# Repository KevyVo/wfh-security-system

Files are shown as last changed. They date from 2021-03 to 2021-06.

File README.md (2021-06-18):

# Work From Home Security System Documentation

## Summary
Due to COVID-19, in early spring my internship was forced to transition into a remote and virtual experience. Whenever I had a meeting, my housemates would find ways to disturb me, whether by knocking loudly, or by walking in unannounced. I searched everywhere for a smartlock that would be able to alert people outside that I was in a meeting. Unfortunately, I could not find anything that fit all my needs. Fortunately, being the engineering student I am, I knew what I had to do. It was time to bring this idea into existince and build it myself. 

<!--- ! This is the scanning picture [Project_Image](https://github.com/KevyVo/Smart-Doorlock/blob/table/Images/finger.jpg) -->
lock

## Table of Contents

1. [Demo/Features](https://github.com/KevyVo/wfh-security-system#demofeatures)
2. [Installation/Instructions](https://github.com/KevyVo/wfh-security-system#installationinstructions)
3. [Cloud Architecture](https://github.com/KevyVo/wfh-security-system#cloud-architecture)
4. [Embedded Software](https://github.com/KevyVo/wfh-security-system#embedded-software)
   1. [High-Level State Diagram](https://github.com/KevyVo/wfh-security-system#high-level-state-diagram)
   2. [Low-Level Flowchart](https://github.com/KevyVo/wfh-security-system#low-level-flowchart)
   3. [User Table Interaction Diagram](https://github.com/KevyVo/wfh-security-system#user-table-interaction-diagram)
   4. [File Structure Directory](https://github.com/KevyVo/wfh-security-system#file-structure-directory)
   5. [Custom Libraries](https://github.com/KevyVo/wfh-security-system#custom-libraries)
5. [3D Printed Parts and CAD Model](https://github.com/KevyVo/wfh-security-system#3d-printed-parts-and-cad-model)
   1. [Front I/O](https://github.com/KevyVo/wfh-security-system#front-io)
   2. [Internal Housing](https://github.com/KevyVo/wfh-security-system#internal-housing)
6. [Electrical](https://github.com/KevyVo/wfh-security-system#electrical-1)
   1. [Wiring Diagram](https://github.com/KevyVo/wfh-security-system#wiring-diagram)
   2. [Wiring Tables](https://github.com/KevyVo/wfh-security-system#wiring-tables)
7. [Materials and Equipment](https://github.com/KevyVo/wfh-security-system#materials-and-equipment)
   1. [Equipment](https://github.com/KevyVo/wfh-security-system#equipment)
   2. [Materials](https://github.com/KevyVo/wfh-security-system#materials)
8. [Troubleshooting and Common Problems](https://github.com/KevyVo/wfh-security-system#troubleshooting-and-common-problems)

## Demo/Features

My work from home security system, aid in alot more ways then just a smart door lock. There would be a live gif and a small explantion for all features:

1.  Remote Arming/Disarming from serverless site</br><details> 
     <summary>Click for Live Demo</summary>
     
     ### Override Trigger
     1. In the gif the main.py file is waiting for a trigger when the user want to diable the alarm system.
        - unlock
     2. In the gif the main.py file is waiting for a trigger when the user want to arm the alarm system.
        - lock
   </details>

2.  Live updates from serverless site</br><details> 
     <summary>Click for Live Demo</summary>
     
     ### Live update
     - Will update all information relating to the last or cuurent state of the door, either by moblie browser or web browser.
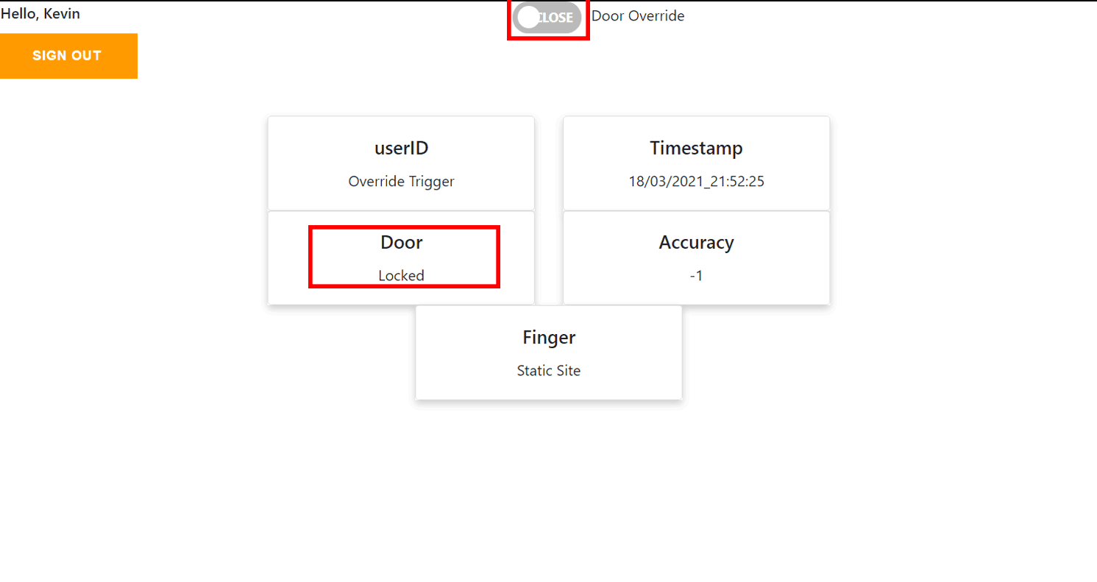
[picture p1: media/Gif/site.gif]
web
       - 
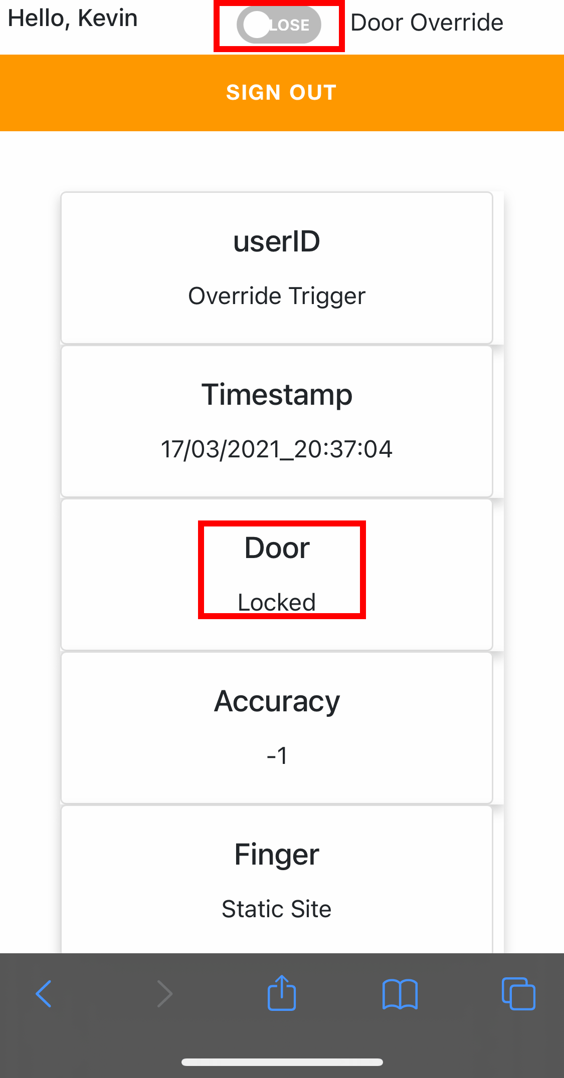
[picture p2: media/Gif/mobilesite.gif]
       - 
   </details>

3.  Google calendar API</br><details> 
     <summary>Click for Live Demo</summary>
     
     ### Google Calendar
     - This will read continously from your google work calendar and alert other outside your door not to distrub during these hours.
       - google
   </details>

4.  Autonomous Motion Light/System Sensor</br><details> 
     <summary>Click for Live Demo</summary>
     
     ### Light/System Sensor
     - The light and security system will turn on with motion and turn off after 5 mins of no activity. The sensor will work in the darkest condtions.
       - dark
   </details>

5.  Biometric Authentication</br><details> 
     <summary>Click for Live Demo</summary>
     
     ### Fingerprint Scanner
     - Authenticate authorize user to gain access to the room with their pre-regsiter fingerprint, the light will also blink a certain colour depending on the assessment. It will also save any fail fingerprint on local storage for identifying potential unauthorized events.
       - Correct Fingerprint (Blink Green)
       - correct
       - Incorrect Fingerprint (Blink Red)
       - Incorrect
   </details>

6.  Excceded Timeout</br><details> 
     <summary>Click for Live Demo</summary>
     
     ### Timeout
     - Will set a timeout of 5 mins after 3 continous authenication failures, every addtion failure will be (timeout= tries * 5 mins). This will reset after one correct authernication. It will also save any fail fingerprint on local storage for identifying potential unauthorized events.
       - timeout
   </details>

7.  Forced Entry Detection</br><details> 
     <summary>Click for Live Demo</summary>
     
     ### Forced Entry Detection
     - Will sound an alarm once the door is open with any proper autheication or break in. The alarm will only turn off once a authenticated fingerprint has reset the alarm.
       - fsd
   </details>

8.  E-mail alerts</br><details> 
     <summary>Click for Live Demo</summary>
     
     ### Alerts
     - There are 3 events that will send e-mails on
      1. Force Entry Dectection Triggered
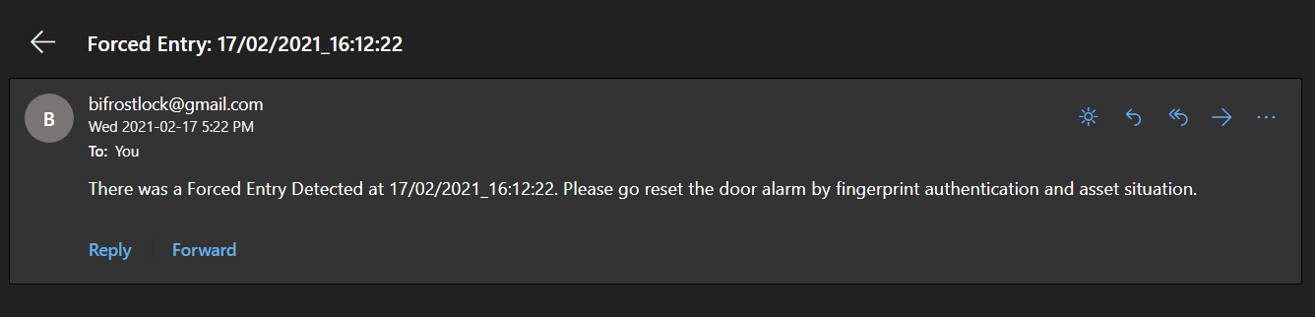
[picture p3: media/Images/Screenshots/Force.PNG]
force
          + 
      2. Correct fingerprint to deactivate the alarm
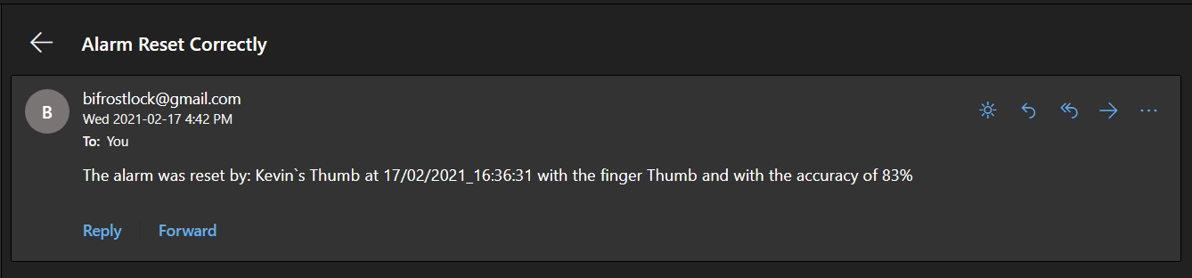
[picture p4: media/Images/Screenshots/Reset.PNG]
reset
          + 
      3. Fail fingerprint with the fail printed attached to e-mail (In real e-mail the fingerprint would not be blurred)
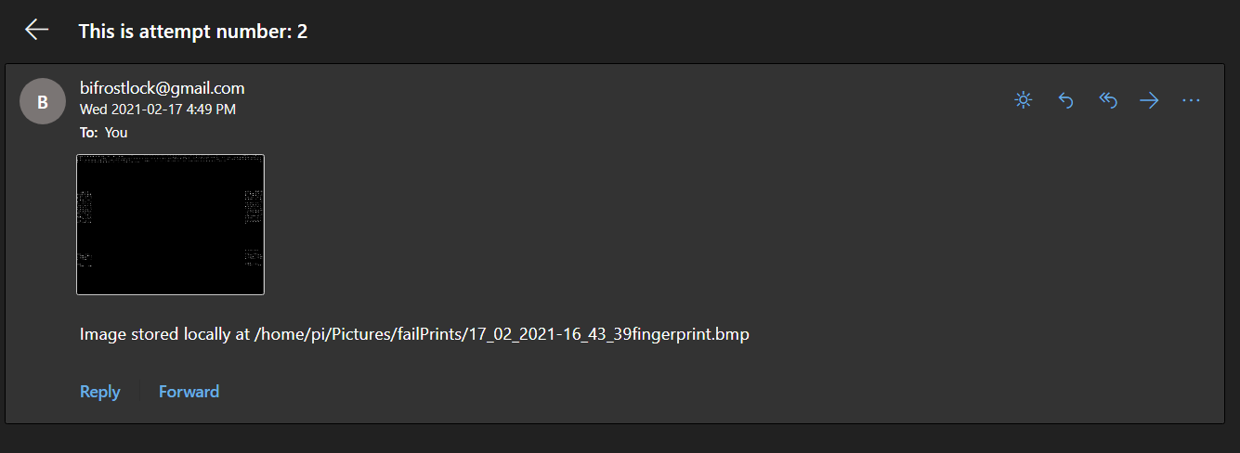
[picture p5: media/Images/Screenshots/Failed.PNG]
fail
          + 
   </details>

9.  Logging events into database</br><details> 
     <summary>Click for Live Demo</summary>
     
     ### Logging
     - Will recored all events of the state of the door in a database for security purposes.
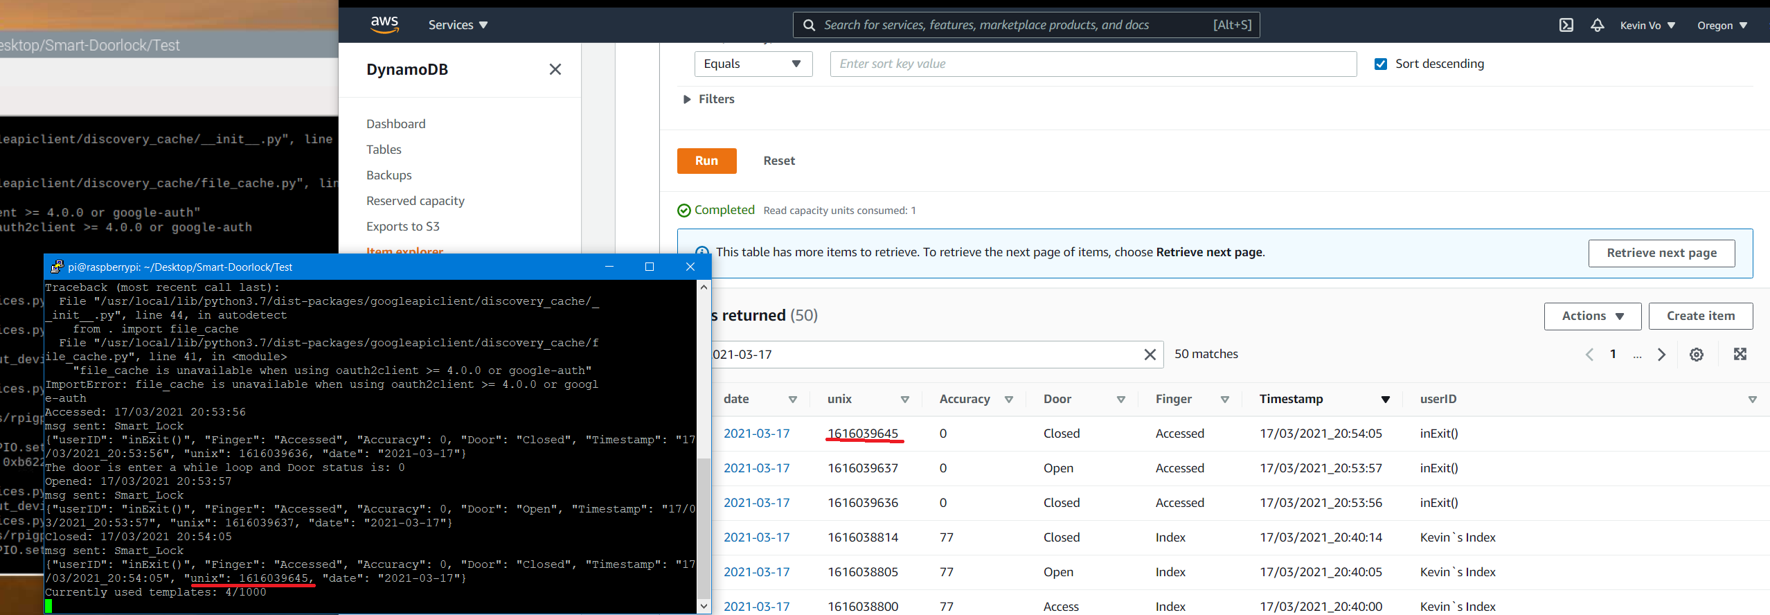
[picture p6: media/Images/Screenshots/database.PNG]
database
       - 
   </details>

10.  Motion alert</br><details> 
     <summary>Click for Live Demo</summary>
     
     ### Logging
     - Red and Green light will blink simultaneously if there is motion on the other side of the door.
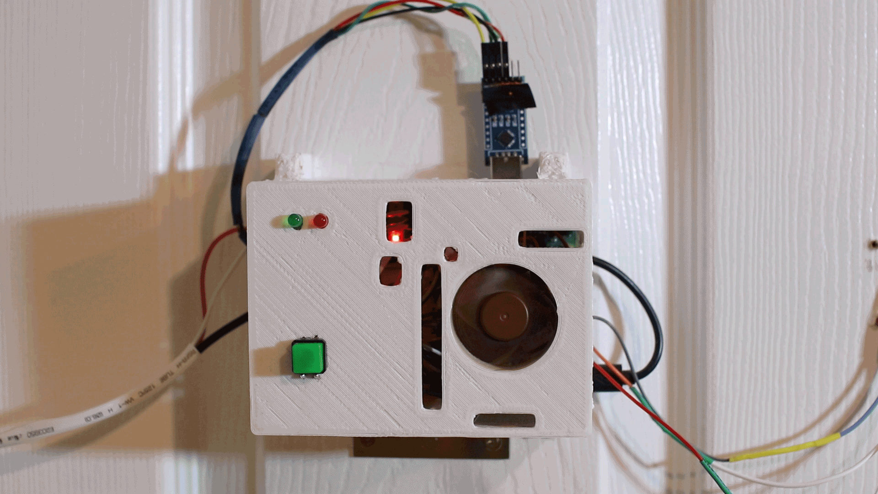
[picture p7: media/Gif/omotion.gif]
motiond
       - 
   </details>

11.  Daytime/Nightime Mode</br><details> 
     <summary>Click for Live Demo</summary>
     
     ### Sound Change
     1.  8AM - 8PM the alarm buzzer will make sound when in use
     2.  8PM - 8AM the alarm buzzer will be disable for nightime use
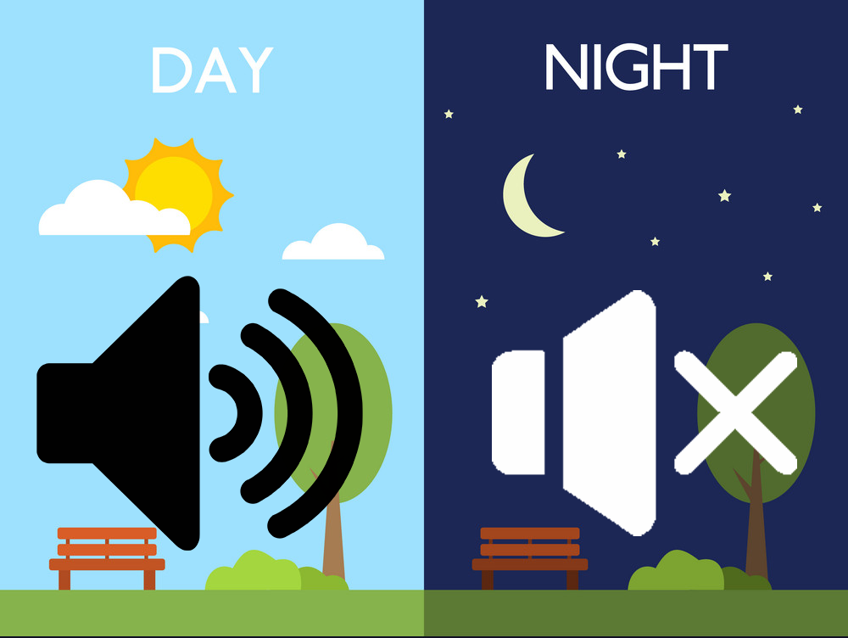
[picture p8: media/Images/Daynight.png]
dn
         - 
   </details>

## Installation/Instructions

**Youtube video**
Coming Soon
<!--- [![IMAGE ALT TEXT HERE](http://img.youtube.com/vi/YOUTUBE_VIDEO_ID_HERE/0.jpg)](http://www.youtube.com/watch?v=YOUTUBE_VIDEO_ID_HERE) -->

Since this project is made up of cloud, electrical and software engineering. I have split up instructions into their own categories to make it easier to follow. 
The React static site has it own separate [repo](https://github.com/KevyVo/wfh-serverless-site), which will appear again in the step below when needed.

Please follow these sequence of instructions in **order** by clicking on the collapsable tabs:</br> **Click on any pictures/GIFs to enlarge them**

1.  <details>
     <summary>Click for General Setup Instruction</summary>
     
     ### General Setup
     1. Gather the materials and make sure you have aquired or have access to the required equipment, found [here](https://github.com/KevyVo/Smart-Doorlock#materials-and-equipment)
     2. Start the 3D print of the Front and Back IO, these prints will take about 1-2 days to 3D print, click here for [files](https://github.com/KevyVo/Smart-Doorlock/tree/master/Cad)
        + There should be 4 total seprate prints
        + These prints will take 1-2 days depending if you deviate from the recommended print settings
        + If you use prusasilcer like me, I highly recommend using these settings here
        + You can find the files here 
     3. Setup the Raspberry Pi
        + RECONMEND: I would use remote access methods like VNC Viewer or SSH, it makes it much easier to control the pi instead of direct connection
        1. Please follow this setup tutorial [here](https://www.tomshardware.com/reviews/raspberry-pi-headless-setup-how-to,6028.html), once completed move onto step b
        2. Please clone this repo to the pi <br/>```git clone https://github.com/KevyVo/Smart-Doorlock ```
        3. cd into the the requirements folder<br/> ```cd Smart-Doorlock/requirments/```
        4. Install the requirements<br/> ```pip install -r require2.txt -r require3.txt```
           + You can also do this inside a virtual environment(venv) if you want
     4. Move onto the Electrical Instructions
   </details>
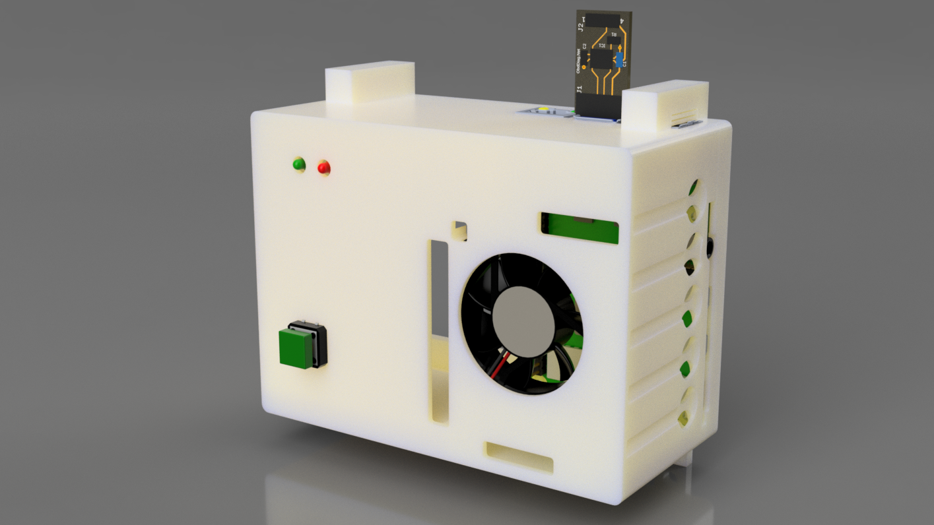
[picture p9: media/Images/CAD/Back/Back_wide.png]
        &nbsp;&nbsp;&nbsp; 

2.  <details>
     <summary>Click for Electrical Instruction</summary>

     ### Electrical

     For a larger image of the wiring diagram and wiring table, please click [here](https://github.com/KevyVo/Smart-Doorlock#electrical-1)

     1. I would recomend testing all of your components indivdially first to see if there are any defects/problems
        1. Go to the Test directory
        2. Select desired component base on the python file
        3. Follow the comment instrutions in the py file of what gpio pins to connect to
        + If the python file does not run in the ide, run it in the terminal using python3 command</br> ```python3 component_name.py```
        + By doing this you will understand how each component behaves and interacts with each other, and assures that it is free of defect
     2. cd into the ```cd Smart-Doorlock/Components/pyfingerprint/example_enroll```
        + I am still working on a feature to enroll your fingerprint using a button on the static- please stay posted! For now, use this method, unless you want to help the project add to it :)
     3. Run the file either in the terminal or ide
        + Congrats! Your fingerprint has been enrolled locally to the system
     4. When connecting the dupoint connectors, make sure you can disconnect the male to female cable apart. This will be useful for mounting installtion later.
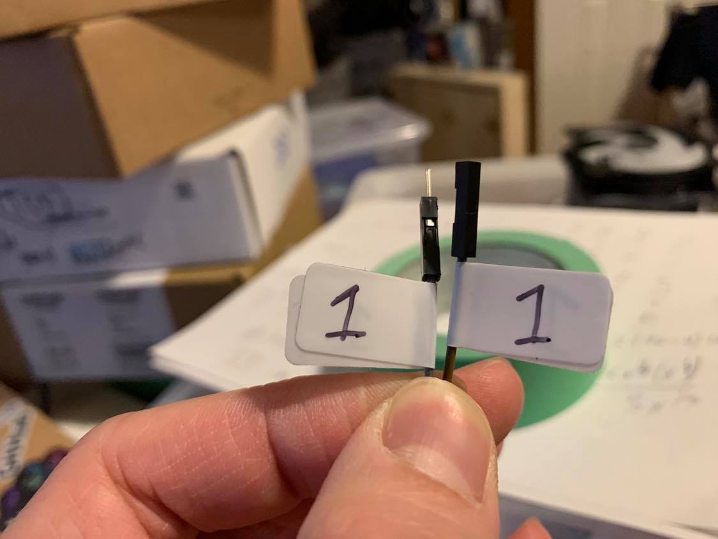
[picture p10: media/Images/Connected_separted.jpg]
        + 
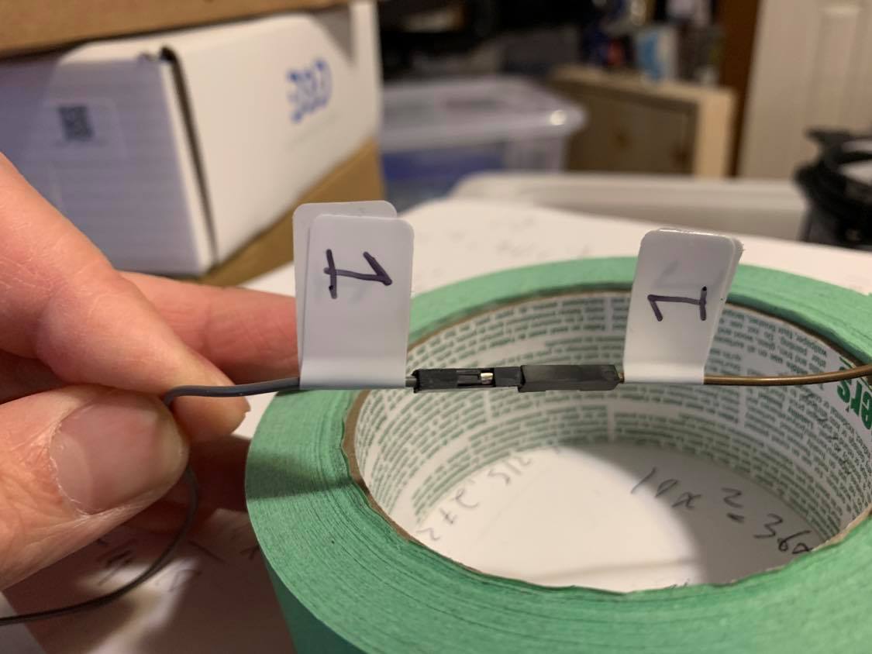
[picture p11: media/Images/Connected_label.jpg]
        + 
     5. Label all cables like this; it make the rewiring installtion easier later on
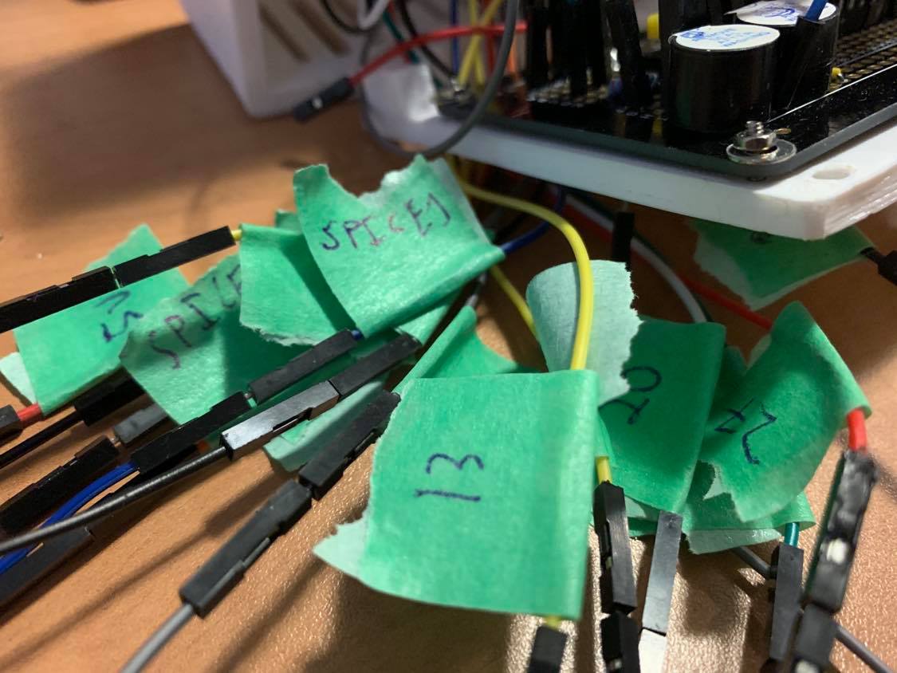
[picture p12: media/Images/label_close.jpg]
        + 
     6. Connect and solder all the electical connections using this diagram and connection tables found here
        + RECOMMENDED: I personally connect all the connections and components on a protyping breadboard before moving onto the solderable PCB
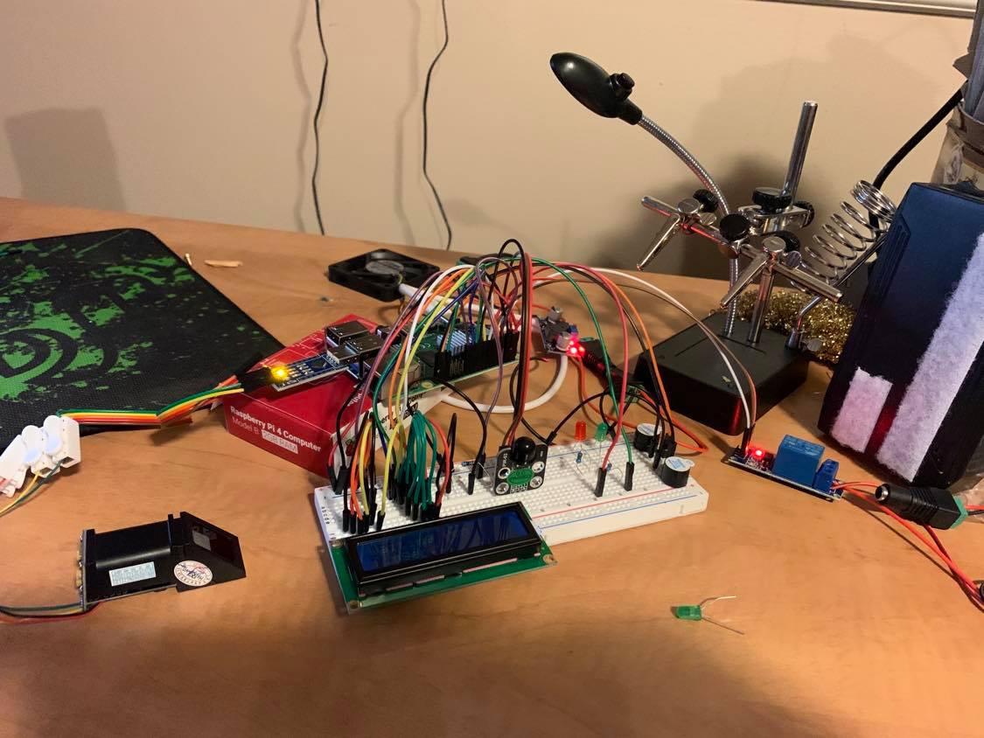
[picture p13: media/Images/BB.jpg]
        + 
        + Run the script ```non-cloud base script```
     7. Run the non cloud base script, to test how all the components will work all together
        + If you see any warnings that do not effect your program, just ignore them for now
     8. If everything was successful please move onto Cloud instructions 
   </details>

   &nbsp;&nbsp;&nbsp; 

3.  <details>
     <summary>Click for Cloud/Software Instruction</summary>

     If you want to read more about how the cloud architecture works please click [here](https://github.com/KevyVo/Smart-Doorlock#cloud-architecture)

     If you want to read more about the flow of the software, please click [here](https://github.com/KevyVo/Smart-Doorlock#embedded-software)

     ### AWS Setup
      1. Sign up for a AWS account (if you already have a account you can skip this step)
         + Follow this [guide](https://docs.aws.amazon.com/polly/latest/dg/setting-up.html) for help if needed 
         + AWS is free if you stay below the free teir limit (we won`t even get close to hitting the limit in this project); AWS is also cheap for personal use if you go over the limit. 
      2. Setup a new IAM user- make sure to give programmatic access and console access and AdministratorAccess policy (you can add the appropriate policy if you know what you are doing)
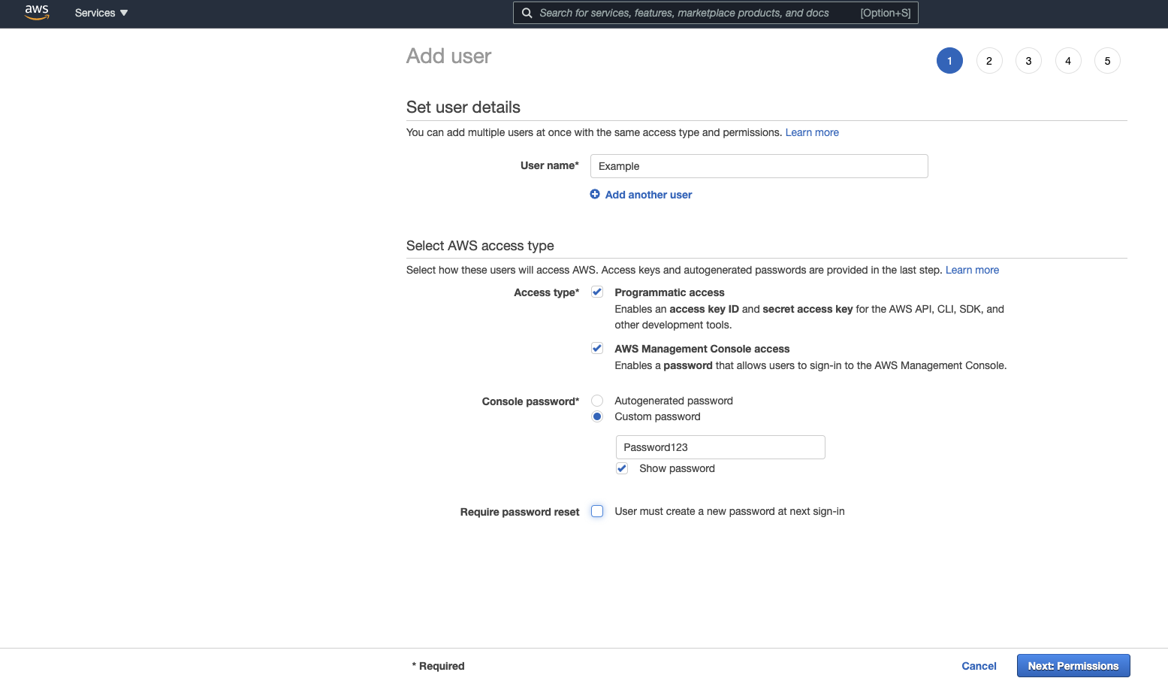
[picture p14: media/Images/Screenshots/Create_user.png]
         + 
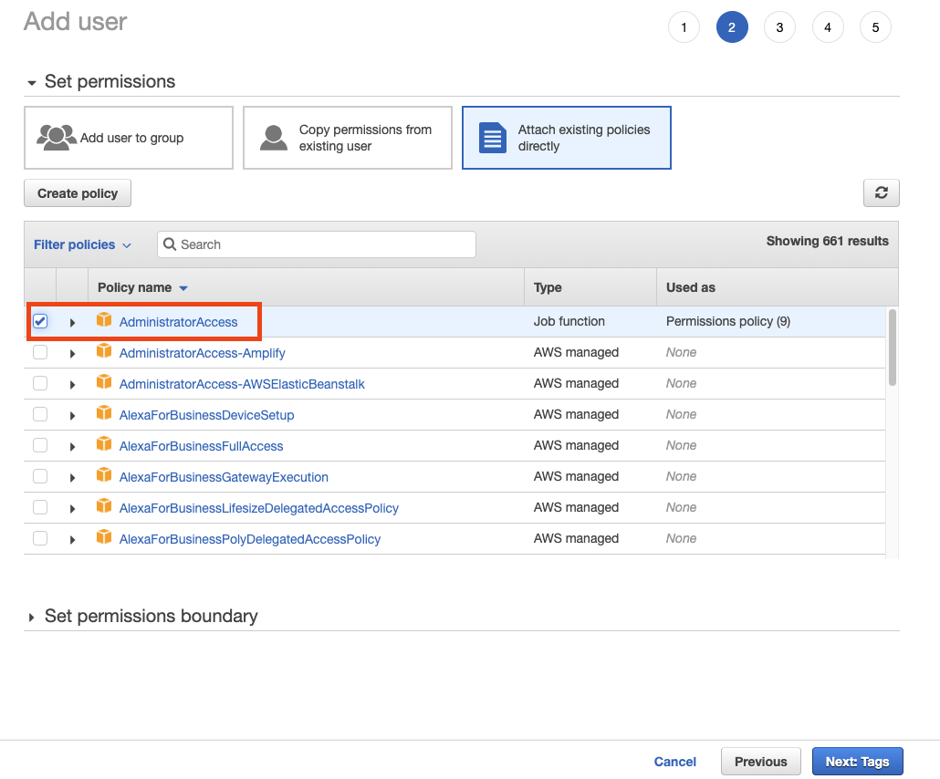
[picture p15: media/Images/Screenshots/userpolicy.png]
policy
         +   
      3. Retrieve the credential for later use
      4. Open up the terminal on the Pi and enter:</br>```aws configure```
      5. Enter that AWS account credentional; please refer to the screenshot for futher assitance and [link](https://docs.aws.amazon.com/polly/latest/dg/setup-aws-cli.html)
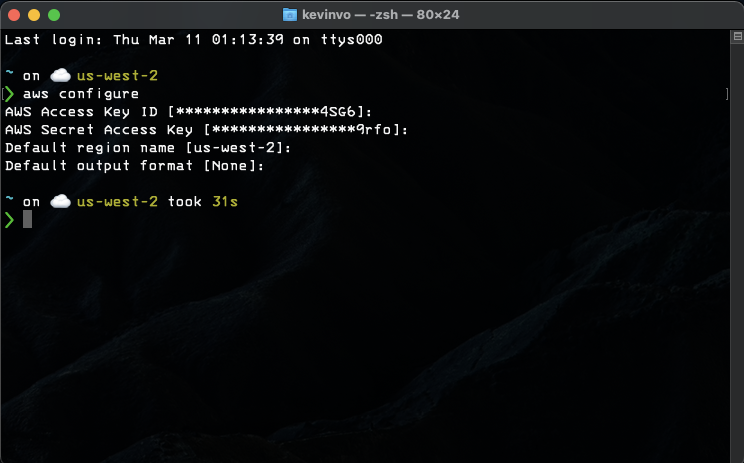
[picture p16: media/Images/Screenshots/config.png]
config
         + 
     ### AWS Iot Core (PubSub)
      1.  We need to sign into the aws console and go to AWS Iot core
      2.  Go to Manage->Things->Regsister a thing
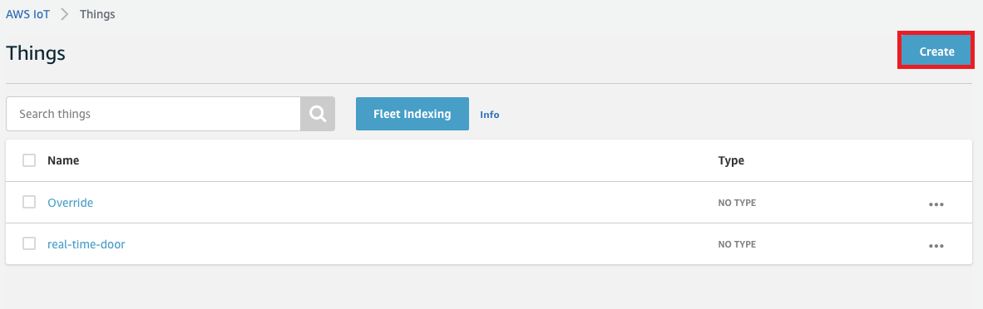
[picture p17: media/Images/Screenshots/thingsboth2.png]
things
          + 
      3.  Click create a single thing and Give your thing name, scroll down and tap on the Next button and then you are immediately offered the one-click certificate generation option. An individual X.509 certificate per device is the recommended way of interacting with AWS IoT services from devices, offering the ability to burn the private key into the device upon enrolment that is then never transferred across the internet alongside requests, a security win. Download the certificate and private key for each device, and also a root CA. Make sure to hit that activate button so the certificate can be used. finish the process by clicking on the “Done” button.
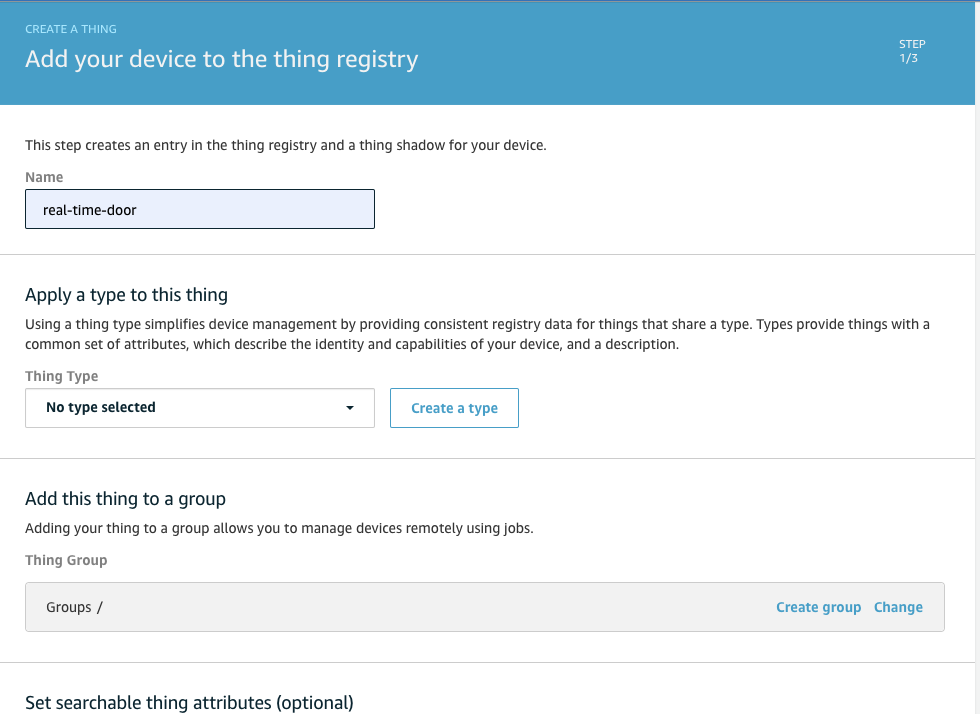
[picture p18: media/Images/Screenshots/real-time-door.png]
          + 
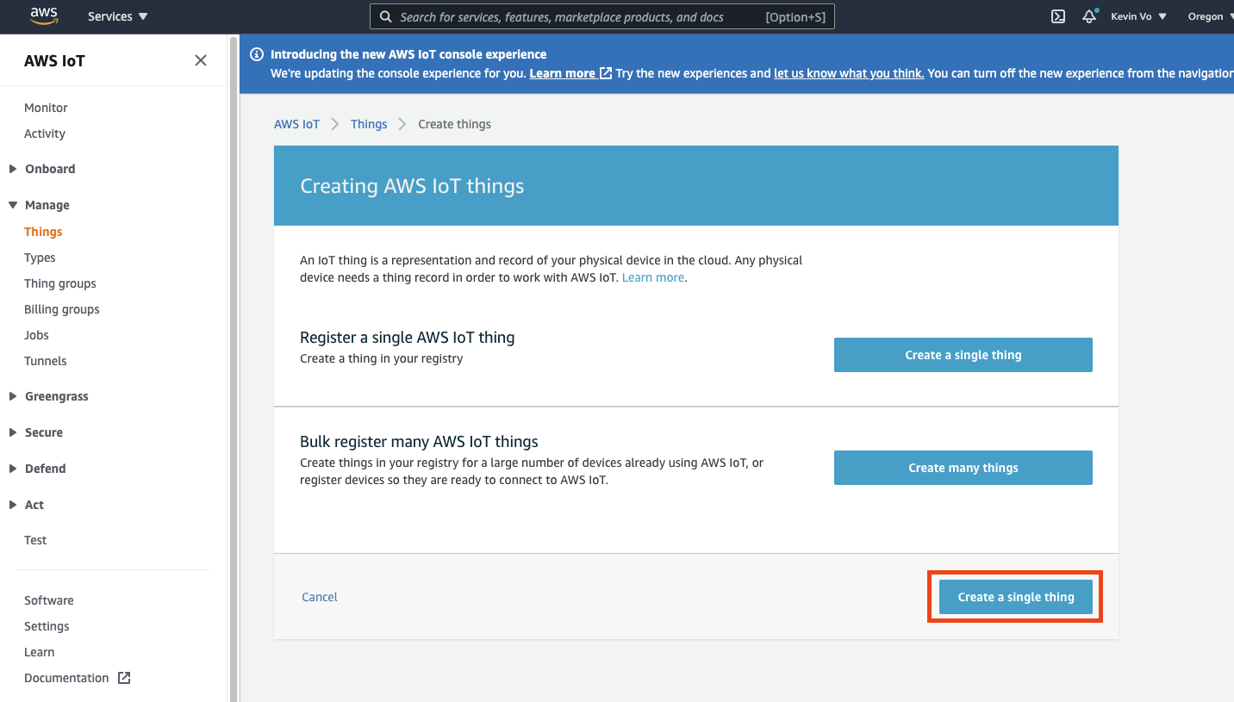
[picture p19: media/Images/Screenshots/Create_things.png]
          + 
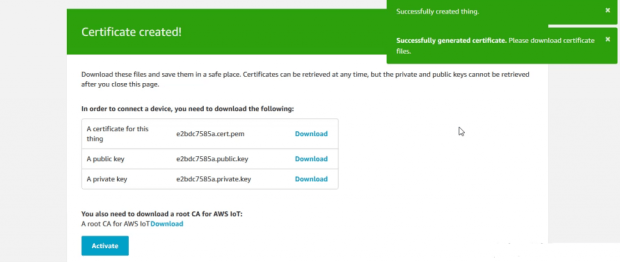
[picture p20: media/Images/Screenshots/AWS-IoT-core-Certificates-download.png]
cert
          + 
      4.  Next point is to create and attach a policy to the certificate, authorizing the authenticated device to perform IoT actions on IoT resources. for this tap on the “secure” tab from the AWS IoT menu which is on the left side, later go for the policies section. Now tap on the button named “Create” which is on the top right corner beside the iot-notifications Icon. give your policy name and fill the fields(Action, Resource ARN ) with a star “*” and check to Allow for Effect option then press the “create” button.
      5.  Now tap on the certificates section which is right above the policies section, You will see a certificate which you have created earlier, tap on the three dots and choose to attach the policy, a pop will come showing your existing policies, check on the recent policy that you have created and attach. That’s it you have successfully created a thing, generated a certificate and attached policy to it.
      6.  You can find the endpoint here
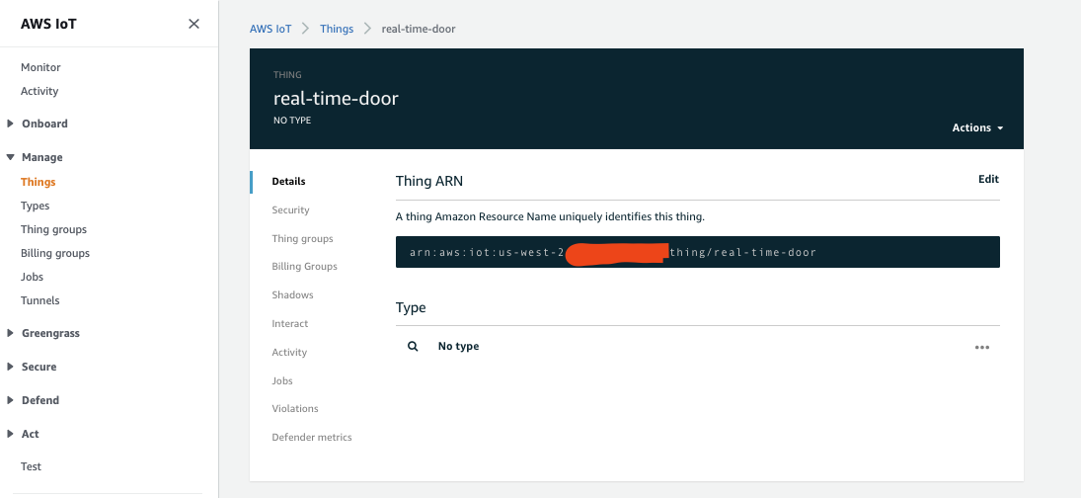
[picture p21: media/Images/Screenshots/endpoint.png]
endpoint
          + 
      7.  I recommend putting all the files/cerficates in the empty directory I premade called "Credtionals"
          + The endpoint can found here
      8.  Fill out the appropriate lines out with the correct pathing in the main.py</br>
            ```
            awshost = "xxxxxxxxxxxxxx-ats.iot.us-east-2.amazonaws.com" # Endpoint
            awsport = 8883 # Port no. 
            clientId = "xxxxxxxx" # Thing_Name
            thingName = "xxxxxxxxxx" # Thing_Name
            caPath = "/home/pi/xxxxxxxx/xxxxxxxx.pem" # Root_CA_Certificate_Name
            certPath = "/home/pi/xxxxxxxx/xxxxxxxx-certificate.pem.crt" # <Thing_Name>.cert.pem
            keyPath = "/home/pi/xxxxxxxx/xxxxxxxx-private.pem.key" # <Thing_Name>.private.key
            ```
      9.  We can test the if the pubsub is working using this script ```python only-pubsub.py```
      10. You should be able to see a Message sent on the ide or terminal when you scan your fingerprint or change the state of the door
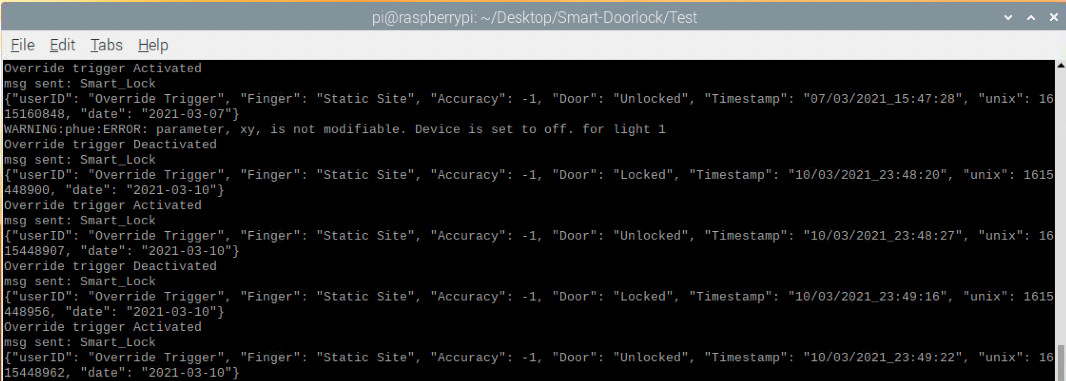
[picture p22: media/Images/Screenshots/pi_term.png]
message
          + 
      11. You can see the data be pushed to AWS Iot core buy going to AWS Iot Core->Test
          1.  Subcribe to topic(it the thingname filled out above)
          2.  Everything can be default
          3.  Hit Subscribe to topic
          4.  You should see a message send like this on your browser
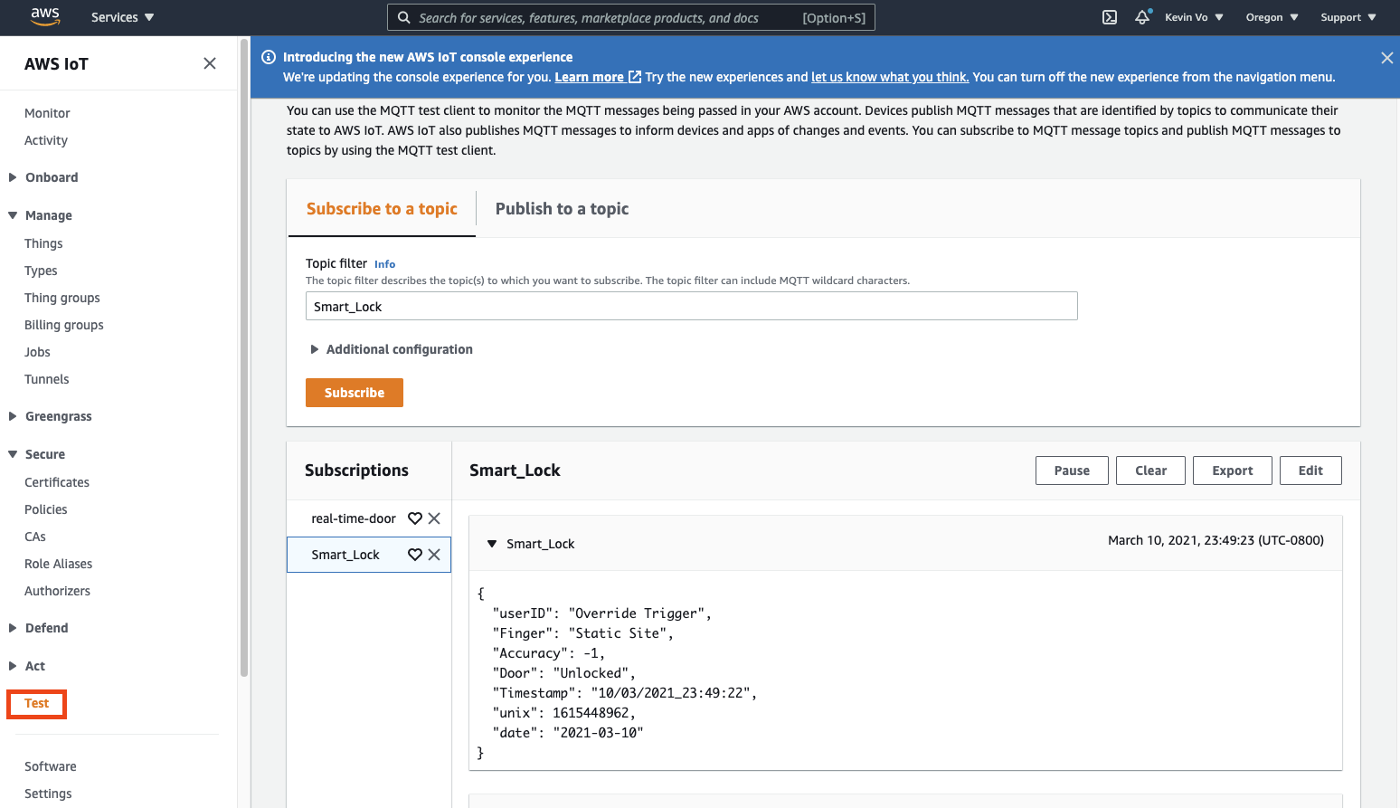
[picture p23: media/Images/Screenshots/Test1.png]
Test
             + 
     ### User Table interaction
     This diagram shows how the User table interacts with the main python script; to learn more about it click [here](https://github.com/KevyVo/Smart-Doorlock#user-table-interaction-diagram)</br>
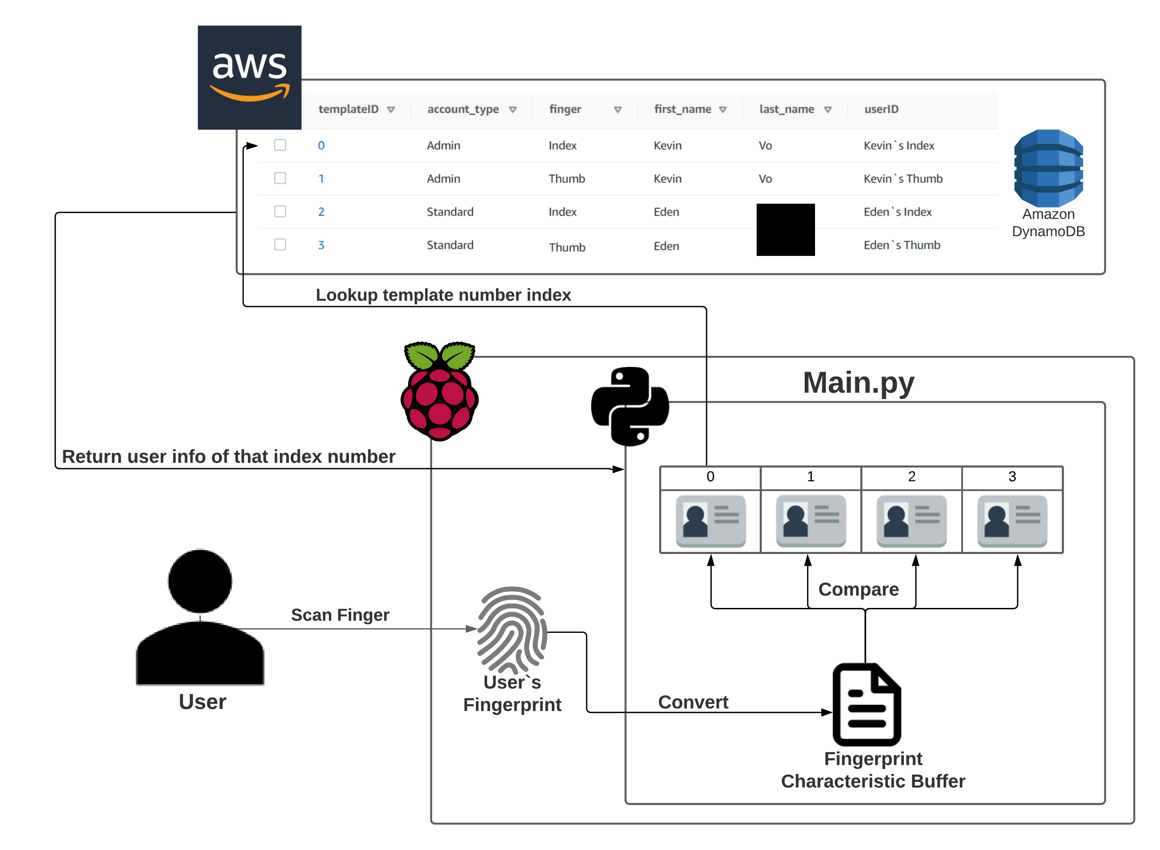
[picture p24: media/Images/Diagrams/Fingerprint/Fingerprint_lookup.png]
      
      - We are going to build this table in the following step
     ### AWS Dynamodb (Database)
      1. Navigate to AWS Dynamodb and make a new Table label: User
         + user
         + This will be the user database, for now you either have to setup the user using the python script or manually using these fields, I am working on add user using the react site on a future feature.
      2. Fill out the parameter of the table like this
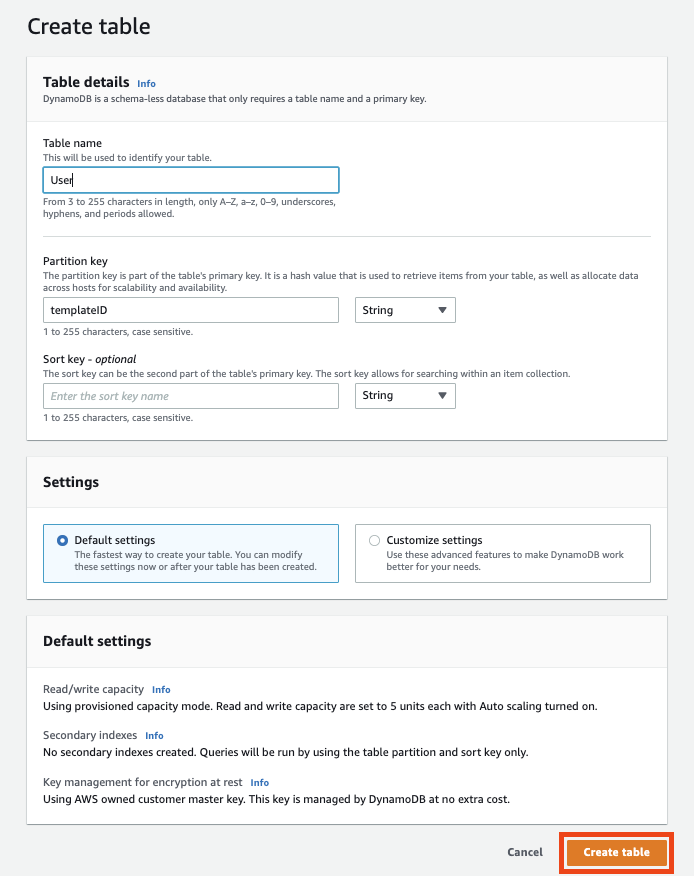
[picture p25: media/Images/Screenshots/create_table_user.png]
para
          +  
          +  Make a diagram of how the user and the fingerprint and the main.py interact with each other
      3. Navgaite to AWS Iot Core->Act and Click on Create a rule
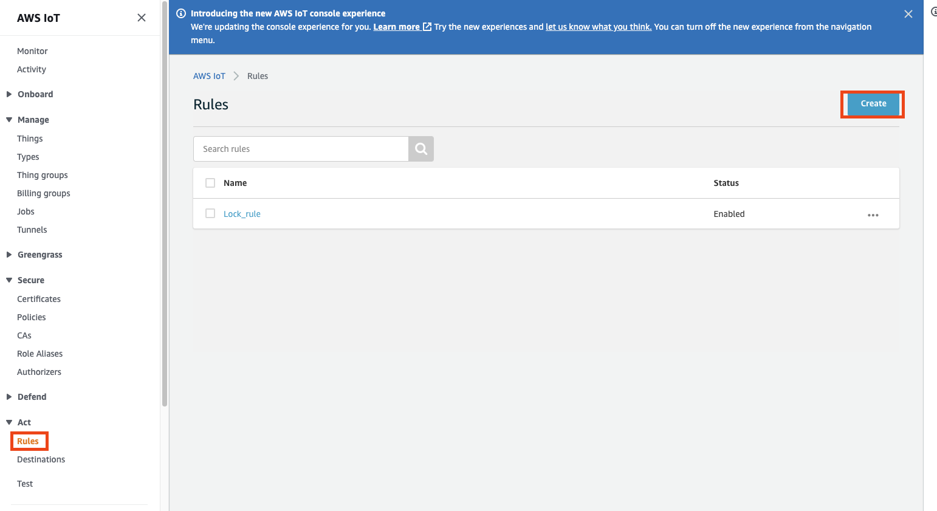
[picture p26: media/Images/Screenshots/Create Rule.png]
create
         + 
      4. Enter ```real-time-door``` for Name
         + real
      5. Under Rule query statement, choose the latest version from the Using SQL version list.</br>For Rule query statement, enter: ```SELECT * FROM `Smart_Lock` ```
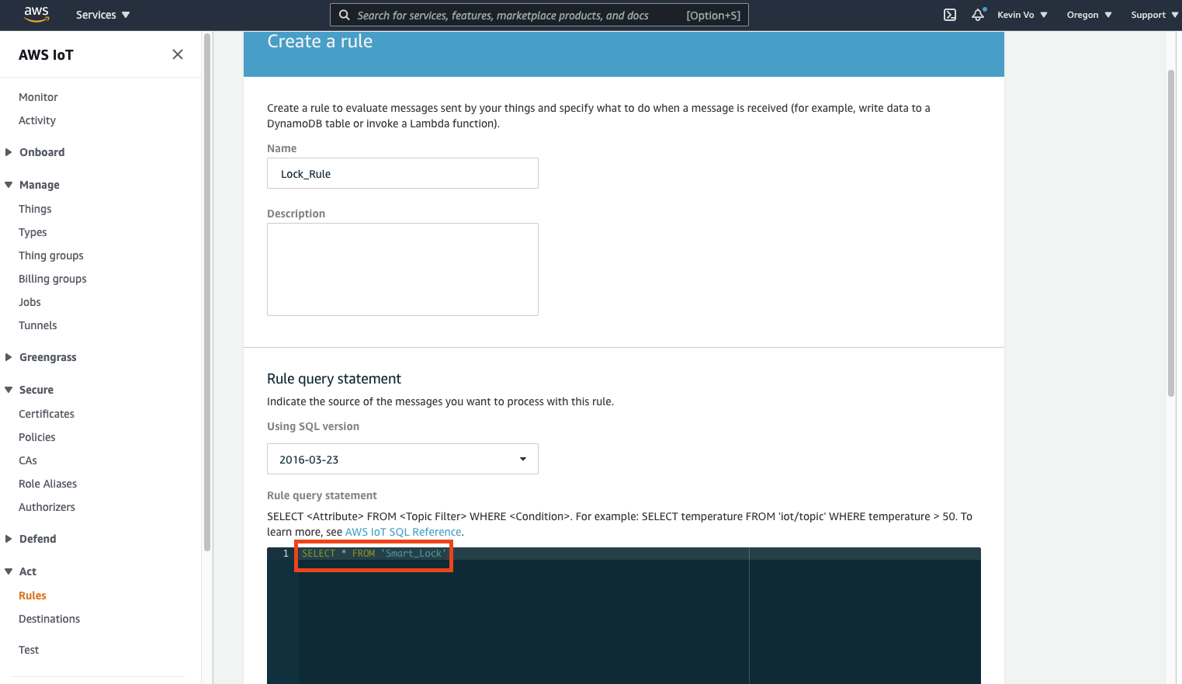
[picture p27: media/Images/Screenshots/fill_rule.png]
ts
         + 
      6. Click add Action
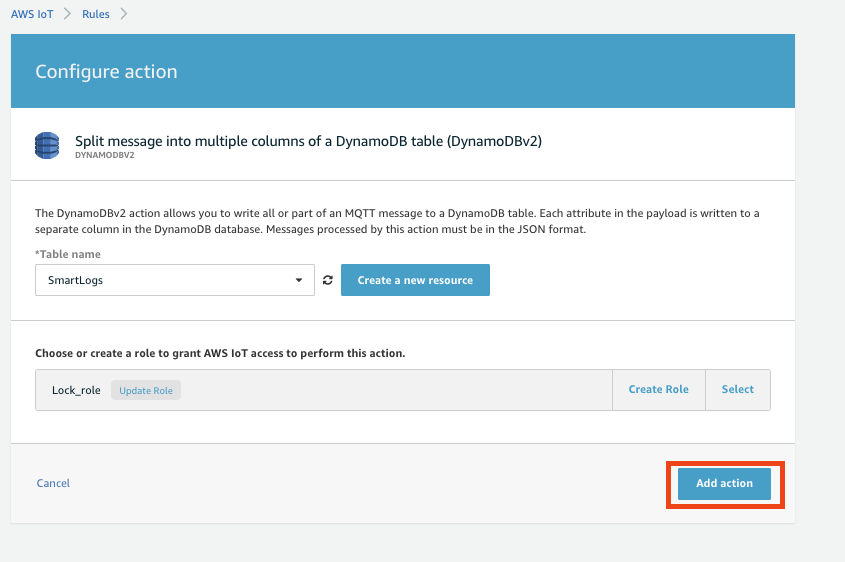
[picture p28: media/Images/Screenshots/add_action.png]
add
         + 
      7. On Select an action, choose to Insert a message into a DynamoDB table and then choose Configure action.
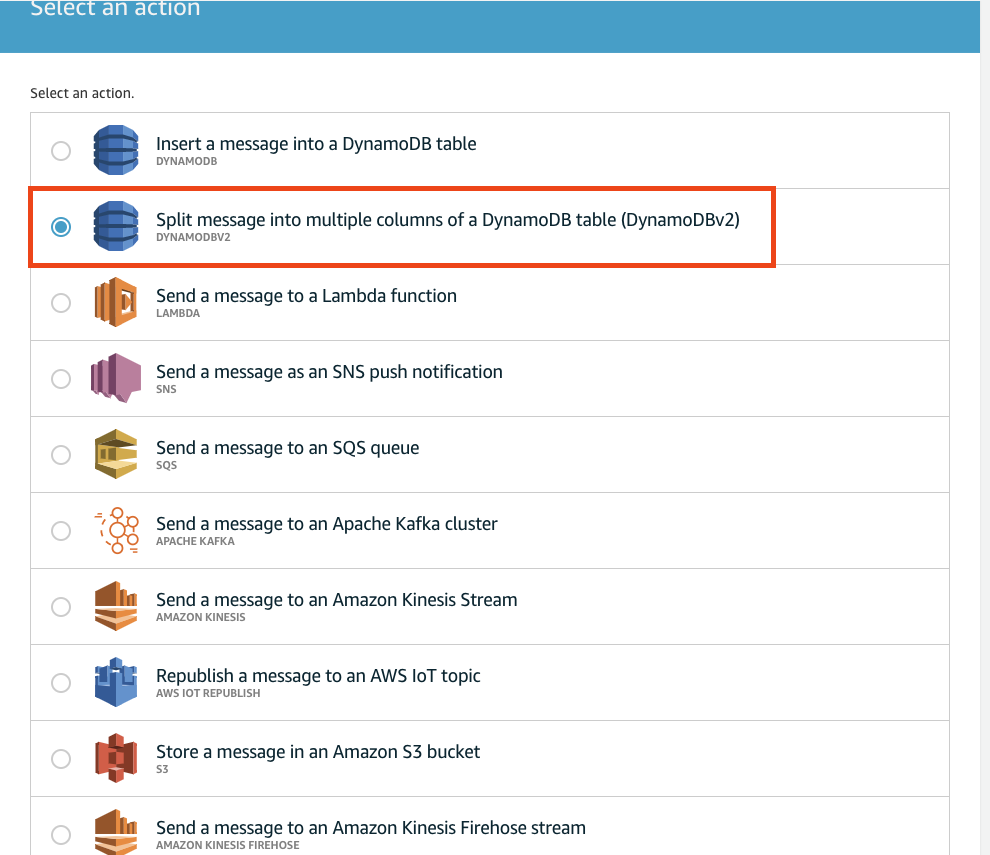
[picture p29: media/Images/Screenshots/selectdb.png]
db
          + 
      8.  On Configure action, choose to create a new resource.
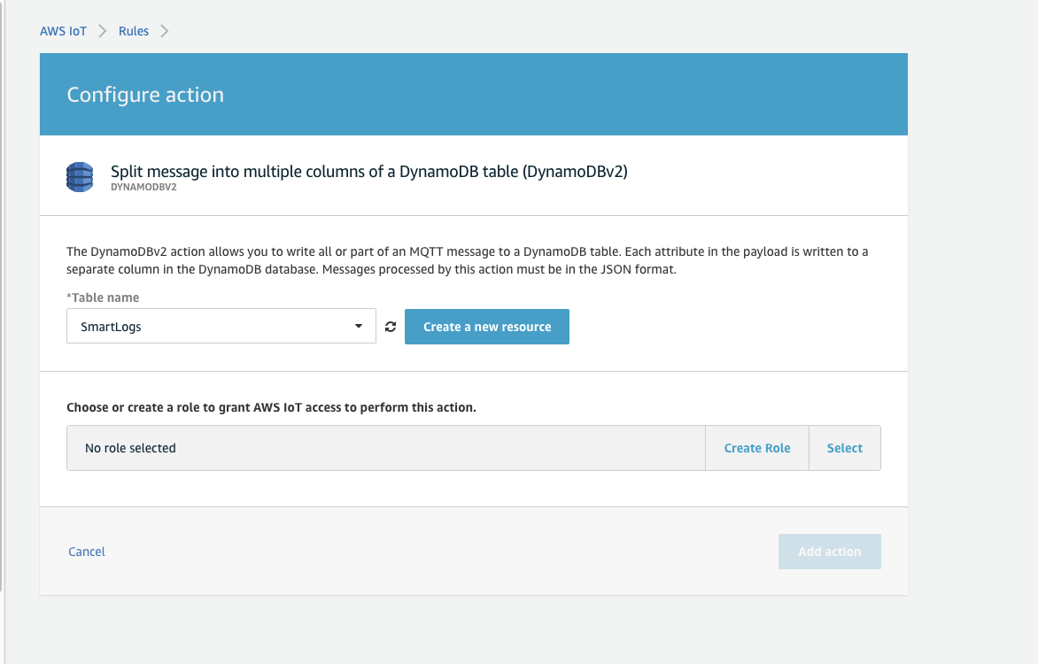
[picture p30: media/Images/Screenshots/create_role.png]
Role
          + 
      9.  On the Amazon DynamoDB page, choose Create table.
      10. When creating the DynamoDB table, enter ```Users``` for table name. In Partition key, enter ```date```. Select Add sort key, and then enter ```unix``` in the Sort key field. Choose String for date (partition Key) and choose Number for unix (sort key) and then check Use Default settings.Now choose to Create as marked in the below screenshot.
          +  I would reccommend follow what I put exactly unless you know what you are doing because my script will being look for these exact key names
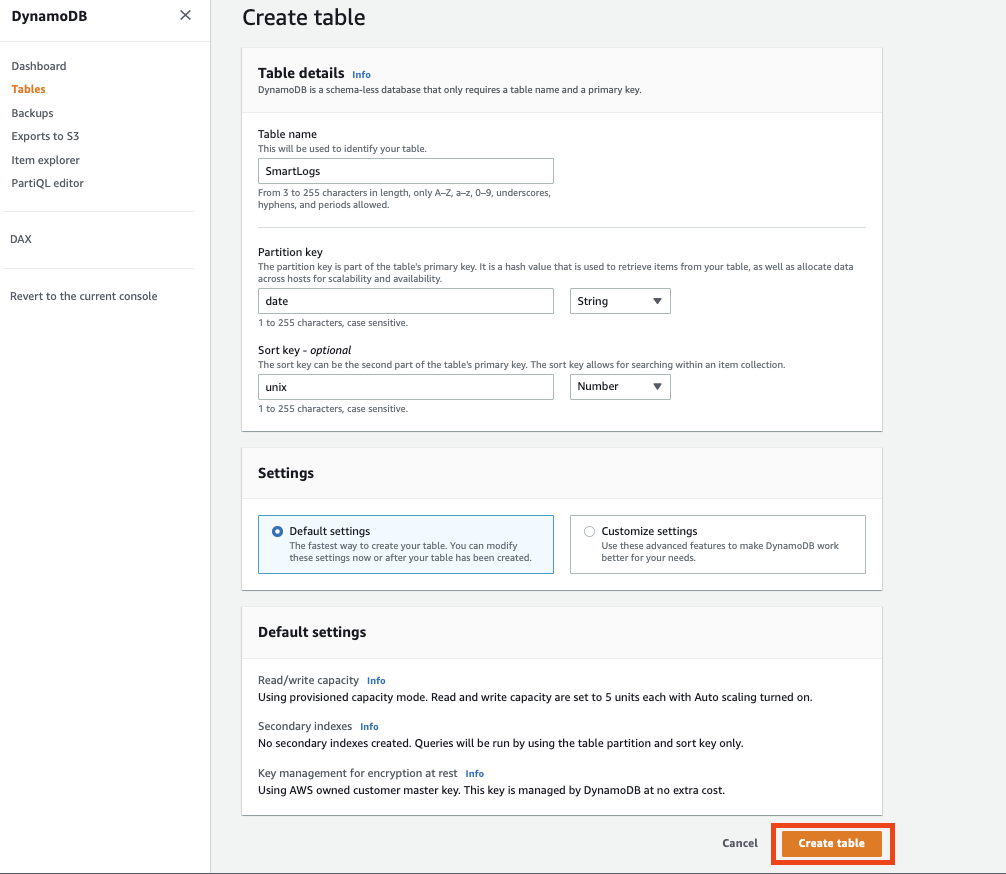
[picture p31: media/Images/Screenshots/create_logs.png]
log
          +  
      11. It takes a few seconds to create your DynamoDB table. Close the browser tab where the Amazon DynamoDB console is open. If you don’t close the tab, your DynamoDB table is not displayed in the Table name list on the Configure action page of the AWS IoT console.
      12. On Configure action, First of all, refresh the resources by clicking on the refresh sign between the Table name drop down and Create a new resource button. Then choose your new table from the Table name list.
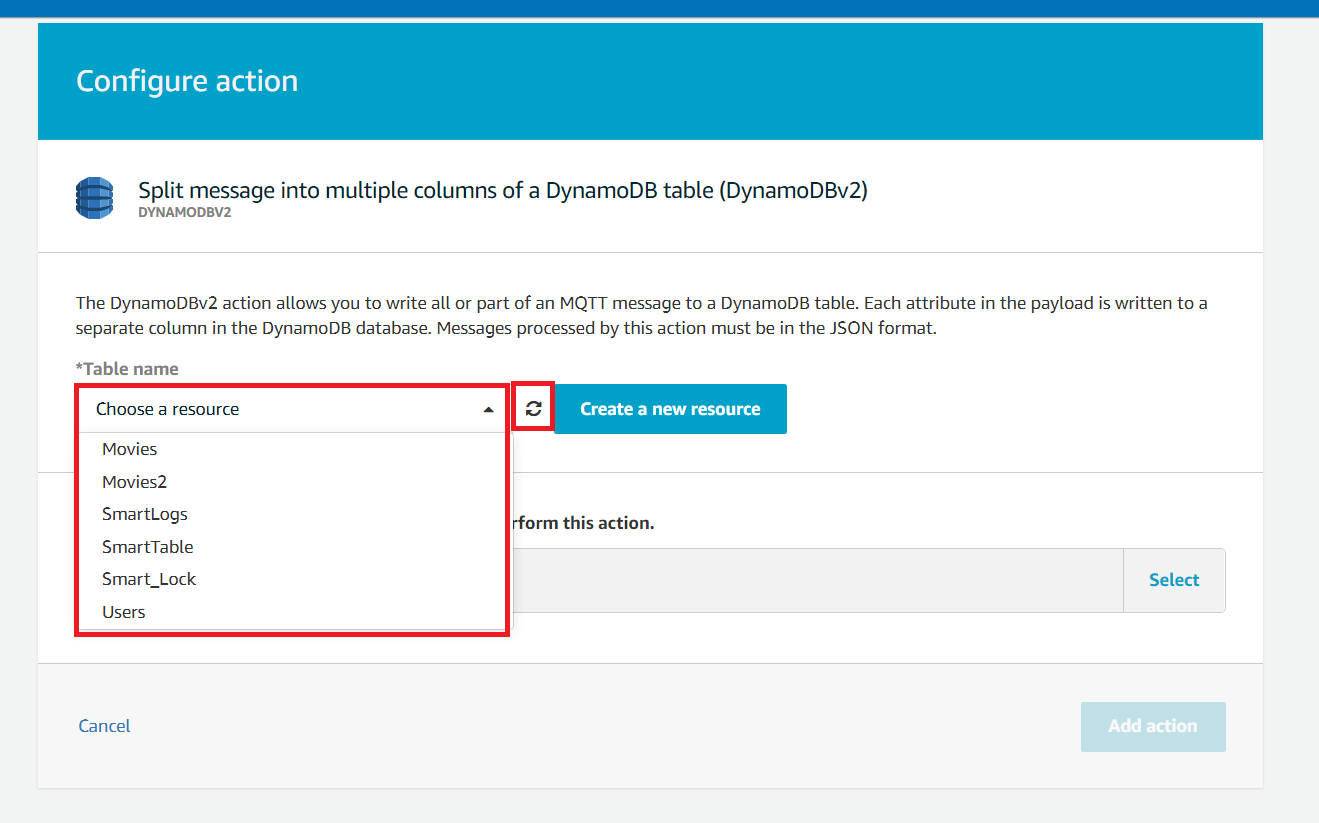
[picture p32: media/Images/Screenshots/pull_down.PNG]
menu
          + 
      13. In Create a new role, enter a unique name, and then choose to Create role.
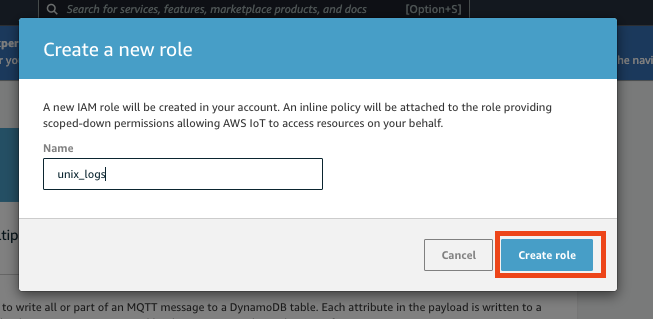
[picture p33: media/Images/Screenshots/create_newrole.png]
role
          + 
      14. Choose Add action
      15. Choose Create rule.
      16. After the successful creation of the rule, you will see the following screenshot.
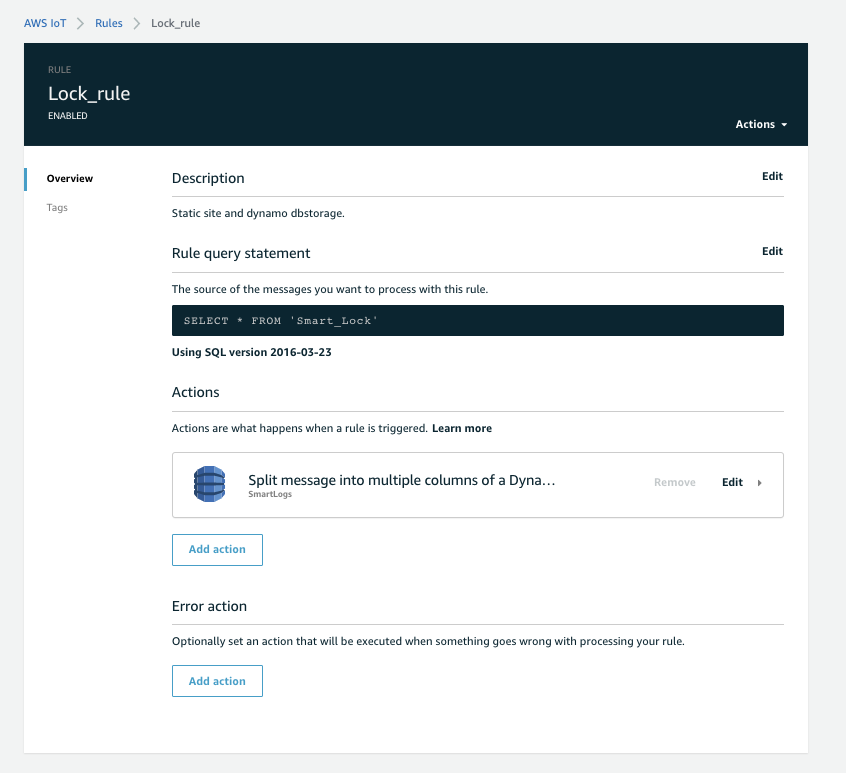
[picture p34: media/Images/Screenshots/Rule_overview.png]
rule
          + 
      17. To see if your AWS Iot Core has logged your events, you can go to AWS Dynamodb and click on the table you just created
      18. Click on items and you will see your last couple of messages that was sent from your pi
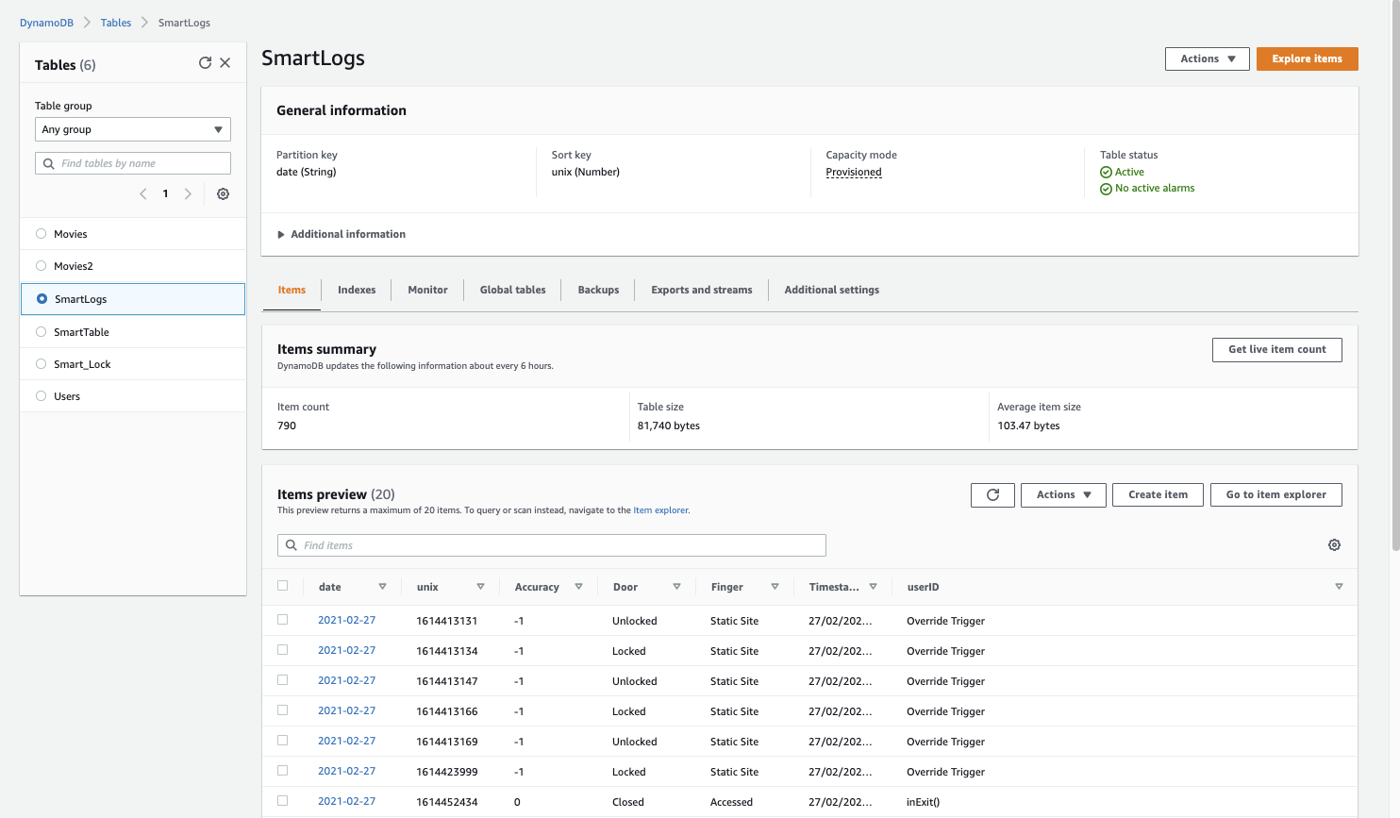
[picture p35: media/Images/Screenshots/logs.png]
logs
          + 

      ### E-mail alert
     **For right now this only work with G-mail account**
      1. Navigate to the file cred/e-mail.txt
      2. Fill out your credtional in the format of the placeholder  and save the text file (This will be the sender e-mail)
      3. Go to the main.py and replace the placeholder of the receving e-mail
      4. If this section was successful you shoud recieve e-mail only for 3 events
         1. Force Entry Dectection Triggered
             + force
         2. Correct fingerprint to deactivate the alarm
             + reset
         3. Fail fingerprint with the fail printed attached to e-mail (In real e-mail the fingerprint would not be blurred)
             + fail
   </details>
      &nbsp;&nbsp;&nbsp; 

4.  <details>
     <summary>Click for Static Site Instruction</summary>
     
     ### Static Site
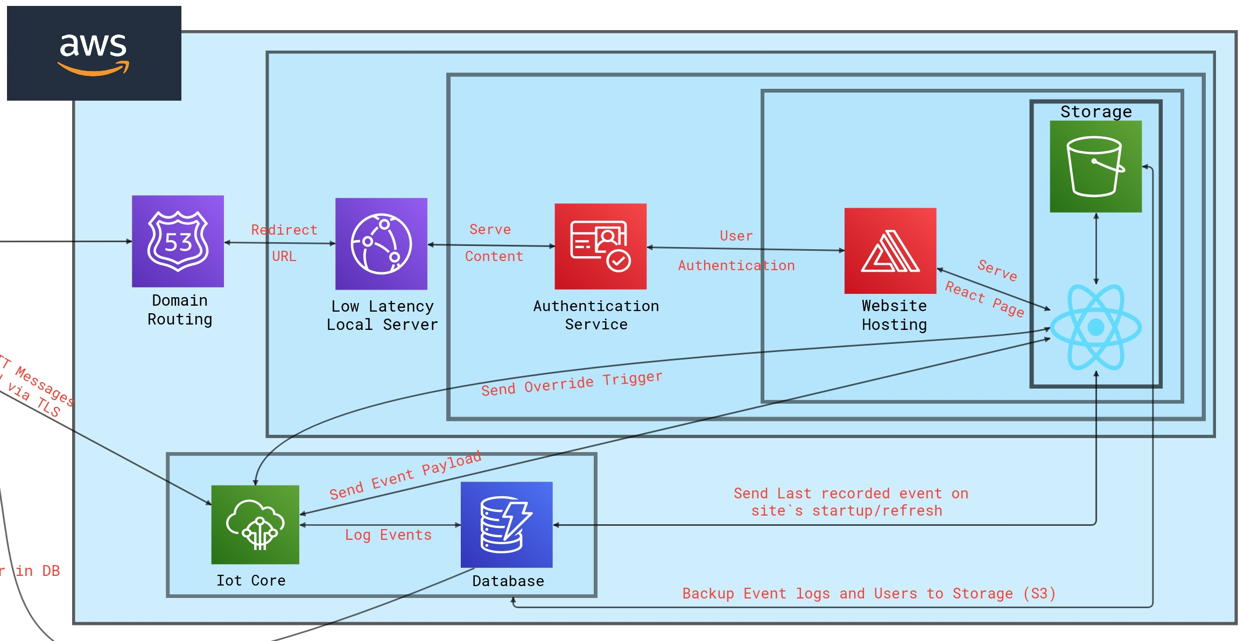
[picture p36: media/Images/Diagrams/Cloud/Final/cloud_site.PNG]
     

     1. Since the static repo had to be a different repo, I have tranfer the instruction for portion onto the static [repo](https://github.com/KevyVo/wfh-serverless-site)
     2. Please return here after completion of the static site repo
     3. Congrats! If everything works, the only thing we still need to do is mount it onto our door. Move onto the Mounting instrutions
   </details>
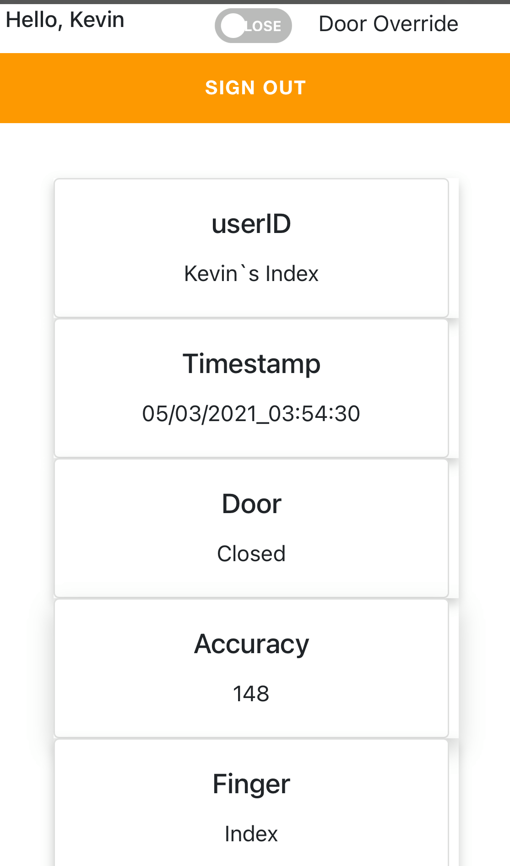
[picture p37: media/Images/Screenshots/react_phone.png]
        &nbsp;&nbsp;&nbsp; 

5.  <details>
     <summary>Click for Smart Lights Instruction</summary>
     
     ### Smart Light Control
     As of now, this device is only compatiable with Philips Hue Lights (mention in Material list)
     1. The lights and Hue bridge should be installed normally with the regular instrutions
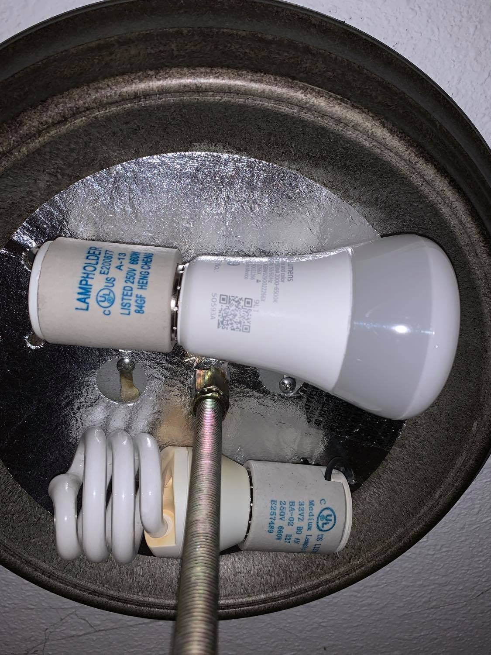
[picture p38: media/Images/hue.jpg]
        +  
     2. You know need to find what is the Hue bridge IP address, there are a couple method on how to find this ip:
        1. Accessing your router using the browser
        2. A windows scanner called [Advanced IP Scanner](https://www.advanced-ip-scanner.com/)
        3. [Nmap](https://www.raspberrypi.org/documentation/remote-access/ip-address.md) scanning
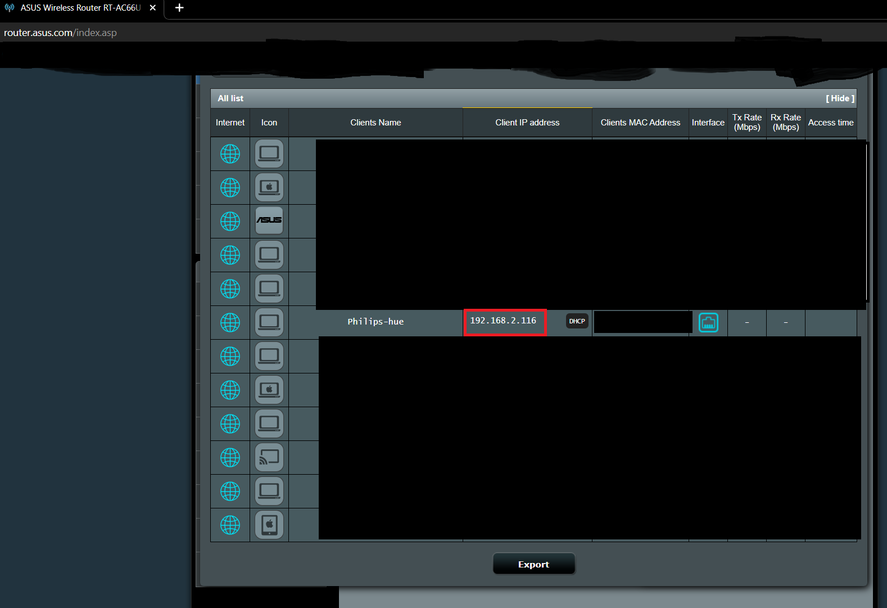
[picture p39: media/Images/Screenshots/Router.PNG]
router
         + 
     3. Make sure that all the lights have recognizeble names on your smartphone app
     4. Call the Hue bridge API by typing this into your browser, URL:</br>```http://<IP>/debug/clip.html``` Use the IP we retrieve above
     5. We need to create user to use the api
        + On the page fill out the parameter like this:</b>
           ```
           URL: /api
           Message Body:
            {"devicetype":"TestApp#RaspberryPi"}
           ```
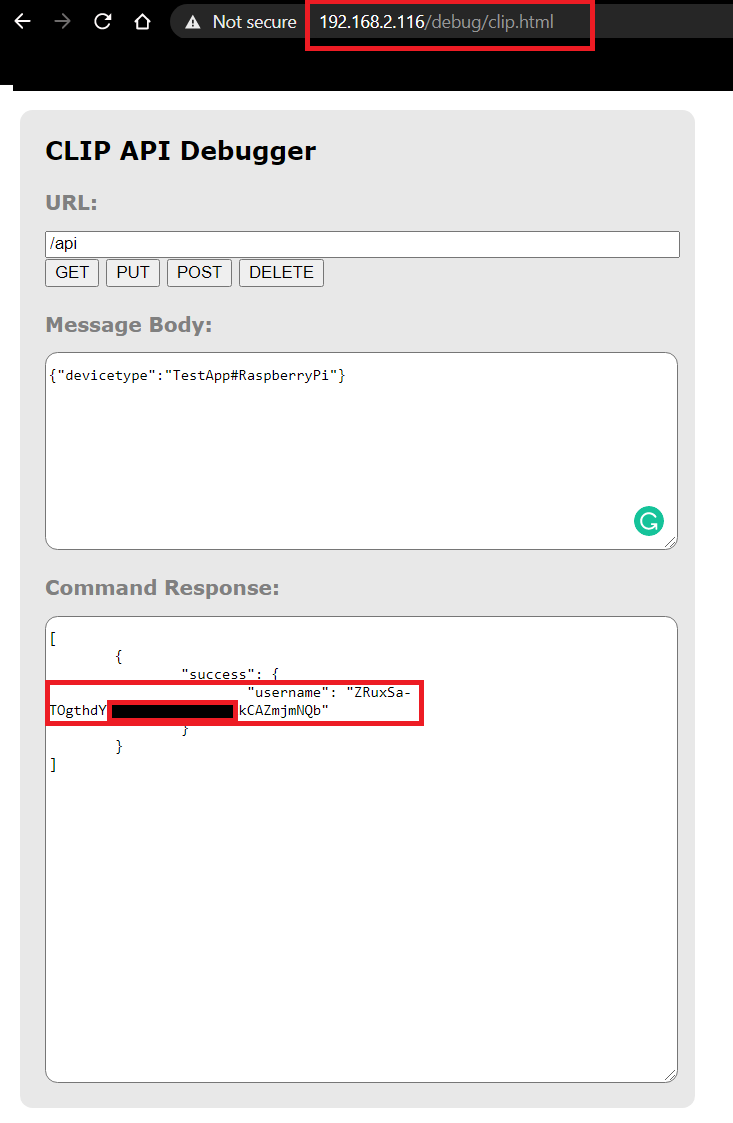
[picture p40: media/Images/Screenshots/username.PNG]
        +       
      1. Press the Hue bridge button, then in the following 30 seconds hit the POST button to run the query
         + bridge
      2. A username should now be generated; please record the username somewhere. We will need this information later.
      3. We will now call all the lights to idenify their names; this will ensure that both lights are connecting with the API
        + Fill in the parameter like this:</br>
          ```
          URL: /api/<username>/lights
          (Replace <username> by the one you got in the previous step (long random string))
          ```
      4. Press the GET button
         + On successful response you should see the names of each light 
         +  
      5.  One last test is to turn off one of the lights
         + Fill ther parameter like this:</br>
           ```
           URL:/api/<username>/lights/2/state
           Message Body:
            {"on":false}
           ```
      6.  Press the PUT Button
          + On a successfull call you should see your light switch off
          +  
      7.  Navigate to ```Smart-Doorlock/Classes/lock_lib.py```
      8.  Open the file in a IDE and replace the placeholder #IP Address with the IP of the Hue bridge 
      9.  Save and close the file
      10. Run the python file ```Smart-doorlock/Test/Smartlightmain.py``` in the terminal
      11. Try unlocking and Locking your door using your fingerprint.<br>The light should flash green on successful fingerprint authention and flash red on incorrect fingerprint
          +  
          + 
      12. If the lights work properly with the python file, move on to the Google Calendar Instructions
   </details>
        &nbsp;&nbsp;&nbsp; 

6.  <details>
     <summary>Click for Google Calendar Instruction</summary>
     
     ### Meeting Detection
     1. Sign into your google account, using the same address as the E-mail alart
     2. Navigate to google calendar and make a differnt calendar called Work
     3. Make a Fake meeting from now until four hours from now. 
       + The title has to contain the word Meeting in it and assign to the work calendar
       + event
     4. Click on this [link](https://developers.google.com/calendar/quickstart/python), You only need to do step one of the google guide by clicking the blue button: Enable the Google Calendar API
       + It will create a new Cloud Platform project and automatically enable the Google Calendar API and make a credentionals.json for us to use
       + blue
     5. Navigate to the directoty and run Smart-Doorlock/G-Cal/gen_pickle.py
       + A window should appear to sign in and give authentican to this python file, it also geneerate a token for future uses
     6. Now we can run the final script
     7. Open a terminal and Navigate then run the file Smart_Doorlock/Src/main.py
       + I found that it runs smoother in the terminal for long term use
       + term
     8. The IO diplay should also know display a active meeting when motion is detected
       +  
     9.  Congrats! The entire system works now, move onto Mounting instrutions
   </details>
        &nbsp;&nbsp;&nbsp; 

7.  <details>
     <summary>Click for Assembly and Mounting Instruction</summary>
     
     ### Assembly
     1. Insert the all components to the front IO like this
      + 
      + 
     2. Use the hot glue gun to keep everything secure, be careful not to touch the 3d print. The heat will burn/damage the print.
      + 
     3. Attach the PCB to the base plate of the door mount
      + 
     4. Attach all the components to the back of the IO like this
      + 
     5. Drill 3 holes on the cover 
     6. Put the 3 x M3 bolts and nuts to secure cover to the base by using the hinge
      + 
      + 
   
     ### Mounting
     1. Pick a spot where you like the housing to be placed and drill a 1/4 inch hole 
        + 
     2. Mount the Front IO to the door using the 4x10mm serews
        + 
     3.  Mount the reed switch to top of the door
     4. + 
     5.  Connect the reed pin to the pi
     6.  Mount the electromagent to the top of the door 
         + 
     7.  Connect the electromagent to the relay
        + WARNING: be careful using a electromagnet, these magnet can seriously hurt you due to the crushing magnetic attraction force
     8.  Attach the Front mounting base to the other side of door and use a level to ensure that it is straight
         
     9.  Route the wires through the hole and push the cover onto base until flush with the door
         
     10. Reconnect the wires using the labels from earlier
          + 
          + I recommend taping a printed sheet of the GPIO to the door while wiring as a reference. This makes it so much easier.
          + 
     11. Connect the Power to usb c on the pi(For now the power will be deliver from the wall, I am looking to making a long lasting battery solution.)
     12. Close the lid, the magnets will attach onto the metal serews holding onto the door
         
     13. Plug in the electromagent power
     14. VNC or SSH into the pi and run the file ```Smart-doorlock/main.py``` in the terminal
     15. Congrats! You have just join the advanced smart security system club. No more bursting into your room!
   </details>
        &nbsp;&nbsp;&nbsp; 

## Cloud Architecture

Cloud_Map

The majority of the web services I used is Amazon Web Services(AWS). Here are the reasons I why I used AWS. Firstly, I was the most comfortable using AWS because of my experience working at Amazon with AWS. Secondly, it has the service AWS IOT Core which the other companies do not offer a PubSub system. You can also used AWS SNS too instead of using the STMP server. I did this because using a STMP server would be free instead of paying for each message send by AWS SNS. The fingerprint files are stored on the local drive of the raspberry for security, instead of being uploaded to S3. My current stack of AWS is free, as I was below the 5GB free teir limit. The only thing I had to pay for was my one time website domain, heimdallr.ca.

## Embedded Software 

### High-Level State Diagram

The diagram represent will how the main.py states change depending on the inputs and sensor data.
You can download/enlarge the image by clicking on it.

High_Level

### Low-Level Flowchart

The flowchart explain every logic decisions in a very low-level.
You can download/enlarge the image by clicking on it.

Flow

### User Table Interaction Diagram
Table
<details>
  <summary>Click for explanation</summary>
  
### Explaintion
1. User scan fingerprint on scanner
2. The fingerprint image get converted into a characteristic text buffer file. The file contain the unqie features of every different fingerprint then stores it into this buffer file.
3. The characteristic file now compares itself to the other key characteristic in the local database. Every different fingerprint file has a index slot that corresponds to it characteristic file.
4. If the buffer file matach over 60% similarity to local characteristic file it will go to the AWS Dyanmodb User Table and lookup the corresponding index number. If not match was found, a value of -1 will be return.
5. AWS Dyanmodb Table will now return all the infomation corresponding to the index number back to the main.py to authenicate the user.

</details>

### File Structure Directory
```
wfh-security-system (root)
├───cad
│   ├───Back
│   │   └───Mk3s
│   └───Front_IO
│       └───Mk3s
├───electrical
│   └───Images
├───libs
│   ├───creds
│   ├───custom
│   ├───phue
│   ├───pyfingerprint
│   │   ├───doc
│   │   └───src
│   │       ├───debian
│   │       │   └───source
│   │       └───files
│   │           ├───examples
│   │           └───pyfingerprint
│   └───raspberrypi-lcd
├───media
│   ├───Gif
│   └───Images
│       ├───Brands
│       ├───CAD
│       │   ├───Back
│       │   └───Front
│       ├───Diagrams
│       │   ├───Cloud
│       │   │   ├───Final
│       │   │   └───Icons
│       │   ├───Fingerprint
│       │   ├───FlowChart
│       │   └───State_Diagram
│       └───Screenshots
├───requirements
├───src
└───test
    ├───Button
    ├───Buzzer
    ├───Calendar
    ├───Combine
    ├───DB
    ├───E-mail
    ├───Lcd
    ├───Led
    ├───Main
    ├───Pir
    ├───Pubsub
    ├───Reed
    ├───relay_lock
    └───Scrap
```

### Custom Libraries

I have created these 7 custom libraries to interact with the main.py file as the main driving file.

1. lcd_lib.py
   - Responsibilty: 
     - Provides a class intake a string and convert it to bits to display the string on the LCD
2. lock_lib.py
   - Dependency: 
     - lcd_lib
     - awsIOT_lib
   - Responsibilty: 
     - Handles all of the locking and re-locking logic
     - Handles all the buzzer sounds and lights sequence
     - Send state messages to AWS IOT Core
3. db_lib.py
   - Responsibilty:
     - Checks if the table exist, if no table then create a new table
     - Retrieve information from tables
     - append items
4. awsIOT_lib.py
     - Responsibilty:
       - Connects to the AWS Iot Core
       - Publish MQTT messages
5. awsIOT_sub.py
     - Responsibilty:
       - Connects to the AWS Iot Core
       - Constantly listen to the command sent from React site
6. GCAL_lib.py
      - Responsibilty: 
        - Connects to the Google calendar api
        - Constantly listen to work calendar for event and event changes 
7. mail_lib.py
      - Responsibilty:
        - Connects to SMTP server
        - Send e-mails from lock e-mail to user email

## 3D Printed Parts and CAD Model

### Print Settings

For Prusasilcer my [3mf](https://github.com/KevyVo/Smart-Doorlock/blob/master/Cad/Front_IO/Mk3s/Front_IO.3mf) file has all of the print settings, just set the machine to other models if you are not using a Prusa i3 MK3s</br>



<details>
  <summary>Click for Cura silcer</summary>

  ### Cura
   - Cura Normal profile
   - Nozzle 0.4mm (haven`t tested other nozzles)
   - Infill density: 20%
   - Skirt: 3 layers
   - Support from build plate only
</details>

<details>
  <summary>Click for other silcers</summary>

  ### Other
   - Support from build plate only
   - Nozzle 0.4mm (haven`t tested other nozzles)
   - Infill density: 20%
   - Skirt: 3 layers
   - First layer speed 20mm/s
   - Perimeters: 45mm/s
   - Infill speed: 80mm/s
</details>

### Front I/O

Click [here](https://github.com/KevyVo/Smart-Doorlock/tree/master/Cad/Front_IO) for CAD files</br>

Click [here](https://github.com/KevyVo/Smart-Doorlock/blob/master/Cad/Front_IO/Mk3s/Front_IO.3mf) for 3mf/gcode for Prusa i3 MK3

**Front**
Frontio

<details>
  <summary>Click for more Photos</summary>
  
**Rear** 
reario

**Waiting for Scan**
scan

**Inside**
inside

**Custom PCB**
PCB

**Print**
print

</details>

---

### Internal Housing

Click [here](https://github.com/KevyVo/Smart-Doorlock/tree/master/Cad/Back) for CAD files</br>

Click [here](https://github.com/KevyVo/Smart-Doorlock/blob/master/Cad/Back/Mk3s/Back.3mf) for 3mf/gcode for Prusa i3 MK3

**Front**

Back

<details><summary>Click for more Photos</summary>
<p>

**CAD Inside**
interalrear

**CAD Rear**
rearmount

**Inside**
open

**Cover**
cover

**Print**
Back

</p>
</details>

## Electrical

### Wiring Diagram

If the image is to small you can click and download the image.
There are also corresposing wiring tables below if the diagram need more clearifcation.
Flow

<details>
  <summary>Click for more Photos</summary>
  
W1

</details>

### Wiring Tables
<details>
  <summary>Click for Stand Alone Components Table</summary>

  BB GND = Breadboard Ground</br>
  BB POS = Breadboard Positive</br>
  PIR = Passive Infor read Sensor
  
| **From** | **To** | **Wire Colour** | **Component** |
|:----:|:----:|:----:|:----:|
|#1(3v3)|Fan Pos|Red|Cooling Fan|
|#9(GND)|Fan Neg|Black|Cooling Fan|
|#29(GPIO 5)|Reed Pos|White|Reed Switch|
|#25(GND)|Reed Neg|Black|Reed Switch|
|#4(5V)|PIR Pos|Red|PIR|
|#7(GPIO 4)|Data|Yellow|PIR|
|#14(GND)|PIR Neg|Black|PIR|
|BB GND|LED GND|Black|LCD|
|BB POS|LED Power|Red|LCD|
|#12(GPIO 8)|DB7|Orange|LCD|
|#16(GPIO 23)|DB6|Grey|LCD|
|#18(GPIO 24)|DB5|Brown|LCD|
|#22(GPIO 25)|DB4|Cyan|LCD|
|#10(GPIO 15)|E|White|LCD|
|BB GND|R/W|Black|LCD|
|#28(ID_SC)|RS|Light Brown|LCD|
|BB GND|V0|Black|LCD|
|BB Pos|VDD|Red|LCD|
|BB GND|LCD1|Black|LCD|
|#40(GPIO 21)|Buzzer Pos|Red|Buzzer 1|
|#39(GND)|Buzzer Neg|Black|Buzzer 1|
|#38(GPIO 20)|Buzzer Pos|Red|Buzzer 2|
|#34(GND)|Buzzer Neg|Black|Buzzer 2|
</details>

<details>
  <summary>Click for Resistor Componets Table</summary>

  BB GND = Breadboard Ground</br>
  R = 10K ohms Resistor 
  
| **From** | **To** | **Wire Colour** | **Component** |
|:----:|:----:|:----:|:----:|
|#36(GPIO 16)|Cathode with R|Green|Green LED 1|
|BB GND|Anode|Black|Green LED 1|
|#37(GPIO26)|Cathode with R|Green|Green LED 2|
|BB GND|Anode|Black|Green LED 2|
|#31(GPIO 6)|Cathode with R|Cyan|Pushbutton 1|
|BB(GND)|Anode|Black|Pushbutton 1|
|#33(GPIO 13)|Cathode with R|Yellow|Pushbutton 2|
|BB GND|Anode|Black|Pushbutton 2|
|#35(GPIO 19)|Cathode with R|Pink|Red LED 1|
|BB GND|Anode|Black|Red LED 1|
|#13(GPIO 27)|Cathode with R|Pink|Red Led 2|
|BB GND|Anode|Black|Red LED 2|
</details>

<details>
  <summary>Click for Muti-Components Table</summary>

  There will be a table for each component in this section.

  BB GND = Breadboard Ground</br>
  BB Pos = Breadboard Postive
  
  ### Relay and Electromagent
| **From** | **To** | **Wire Colour** | **Component** |
|:----:|:----:|:----:|:----:|
|#11(GPIO 17)|Relay Data|Blue|Pi-Relay|
|BB Pos|Relay Pos|Red|Pi-Relay|
|BB GND|Relay Neg|Black|Pi-Relay|
|Electromagenet Pos|Middle Relay Slot|Red|Relay-Electromagent|
|Electromagenet Neg|Normally Closed(NC)|Black|Relay=Electromagenet|
---
  ### CP2102 and FPM10A (Serial to Fingerprint Scanner)
| **From** | **To** | **Wire Colour** | **Component** |
|:----:|:----:|:----:|:----:|
|3v3|Positive|Red|CP2102-FPM10A|
|Rx|Rx|Green|CP2102-FPM10A|
|Tx|Tx|Blue|CP2102-FPM10A|
|GND|GND|Black|CP2102-FPM10A|
</details>

## Materials and Equipment

### Equipment

If you do not own a 3D printer, there are many other ways you can gain access to one. 

Here are some possible options:
1. A University or School, most places of education now provide 3D printer for use
2. A community center
3. A friend or a famliy member
4. A maker space
5. A online/local printing service

<details>
  <summary>Click for Equipment list</summary>

  If you like to buy some of these items please consider helping support me by buying them through my affiliate links, they would be the same low price either way you purchase them.

+ [3D Printer](https://shop.prusa3d.com/en/3d-printers/180-original-prusa-i3-mk3s-kit.html) (This is the one I have, not a affiliate link)
+ [Wire Strippers](https://amzn.to/3cOpjAx)
+ [Hot Glue Gun](https://amzn.to/38X5VjR)
+ [Soldering Iron/ Soldering Station](https://amzn.to/3vGZ0Vy)
+ [Needle nose pliers](https://amzn.to/30ZeN3T)
+ [Wire cable cutter](https://amzn.to/3eXYLQ3)
+ M3 hex wrench (Usually comes with machine screws)
+ [Metal Pick](https://amzn.to/3cR56tL) (optional, used for support removal) 
+ [Serewdriver](https://amzn.to/311wsrC)
+ [Power drill](https://amzn.to/38X4iTh)
  + Philips head attachment (from screwdriver)
  + [1/8 inch drill bit](https://amzn.to/3vLtjuu)
  + [1/2 inch hole saw attachment](https://amzn.to/3f19h98)

</details>

---

### Materials

I do recommend in just using old parts from pervious projects or leftover from bulk orders. You can try to also find some from a friend or school as well.

If you like to buy some of these items please consider helping support me by buying them through my affiliate links, they would be the same low price either way you purchase them.

<details>
  <summary>Click for Materials list</summary>

1. [Raspberry Pi 4 or 3B+](https://amzn.to/38TmEo7), any GBs is fine (I recommend pi 4)
2. [CP2104](https://amzn.to/3eXKZwI) USB to UART 
3. A Pack of [Dupoint connectors](https://amzn.to/3cKZMZ0) 
4. A set of [22 gauge wires](https://amzn.to/38ZHdiB) 
5. [3D printing Filament](https://amzn.to/3tCKHzE) (I used PLA)
6. [Red LEDS](https://amzn.to/2ONz9uo) x 2 pieces
7. [Green LEDS](https://amzn.to/2ONz9uo) x 2 pieces 
8. 40mm x 40mm [Fan](https://amzn.to/3cRCXmq) 
9. 1 [Heatsink](https://amzn.to/390brC7)
10. 5V 3A [power supply](https://amzn.to/3eXT1WA) for raspberry pi 4
11. [Electromagnet](https://amzn.to/3tB2BTg)
12. [Reed switch](https://amzn.to/2OSEgcX)
13. [Pushbutton](https://www.adafruit.com/product/1010)
14. [USB type C](https://amzn.to/30WdBhK) for raspberry pi power 
15. [Fingerprint scanner](https://www.aliexpress.com/item/33040809031.html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) (FPM10A)
16. [Solderable prototyping PCB](https://amzn.to/2OSPazp)
17. [1602 LCD](https://amzn.to/2P4pzDj)
18. [PIR sensor](https://amzn.to/31cOPKB)
19. [Passive Buzzers](https://amzn.to/3c3QCI8)
20. [Relay](https://amzn.to/38YKgri)
21. A set of 10K [resistors](https://amzn.to/3cTqP4e)
22. Small [hinge](https://amzn.to/3eUgYy1)
23. 8mmx3mm [magnets](https://amzn.to/3918Nfk) x 2 pieces
24. [Philip Smart Lights](https://amzn.to/3eXXYi3)
25. All the screws sizes and quantity 
    - [M3](https://amzn.to/2Qi4969) x 8mm Socket head x 8 pieces 
    - [7mm washers](https://amzn.to/3cIhA6U) x 4 pieces 
    - [#8](https://amzn.to/2PaIg8g) x 5/8 inches wood screws x 8 pieces 
    - Hinge screws comes with the hinge set 

</details>

## Troubleshooting and Common Problems
 
 blah blah blah :)

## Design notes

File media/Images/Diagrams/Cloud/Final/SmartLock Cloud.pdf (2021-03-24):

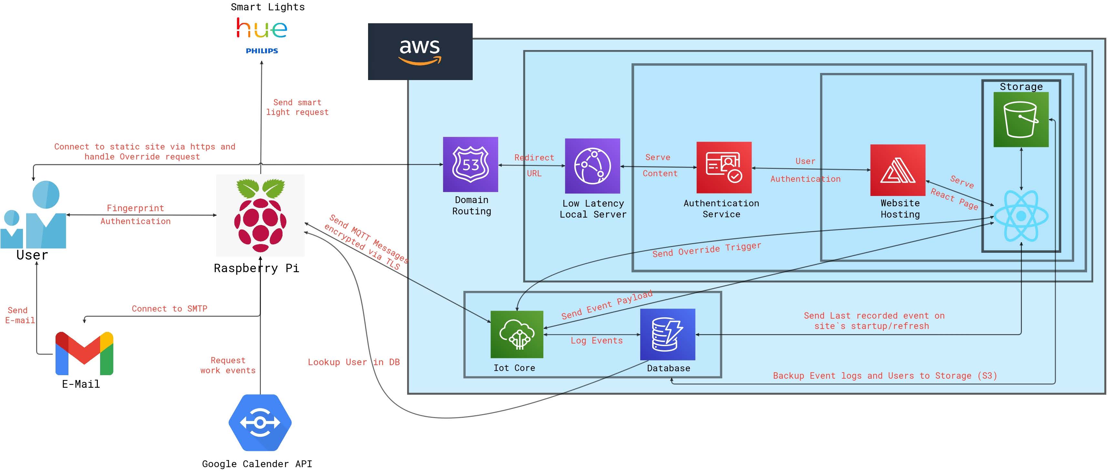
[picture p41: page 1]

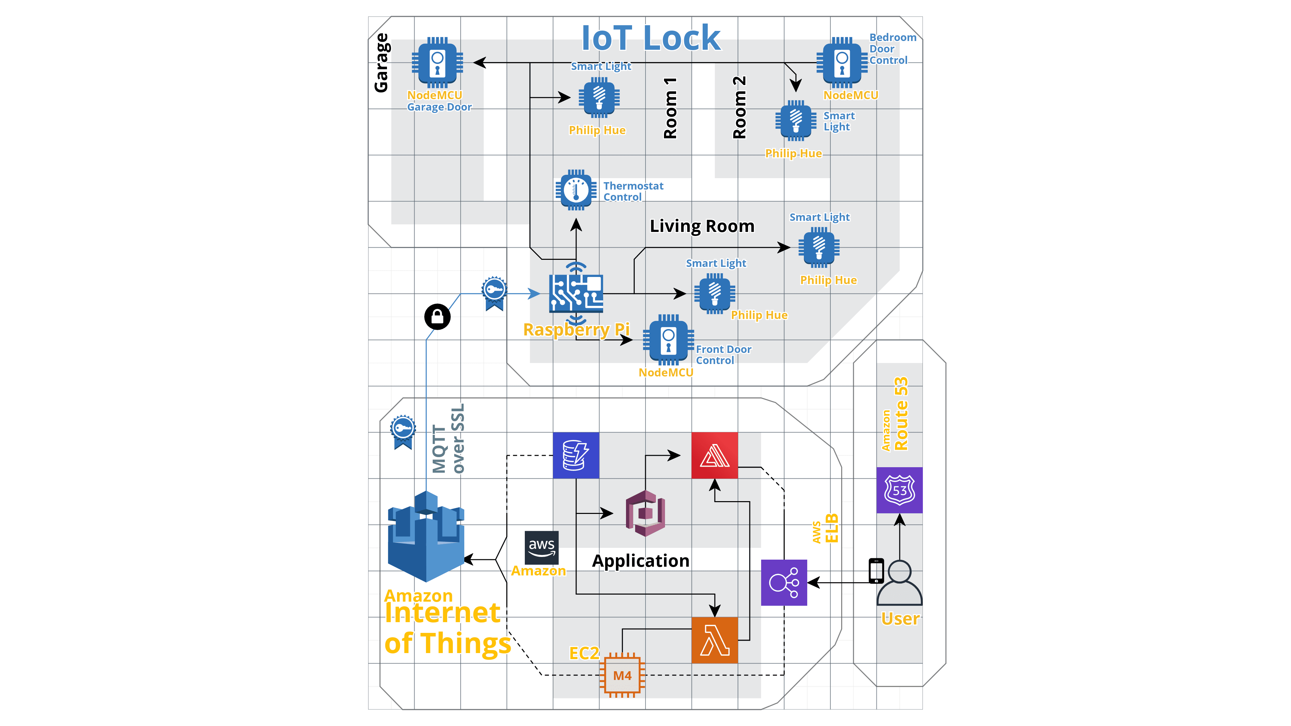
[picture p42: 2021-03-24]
media/Images/Diagrams/Cloud/LockDoor_Architecture_grid.png

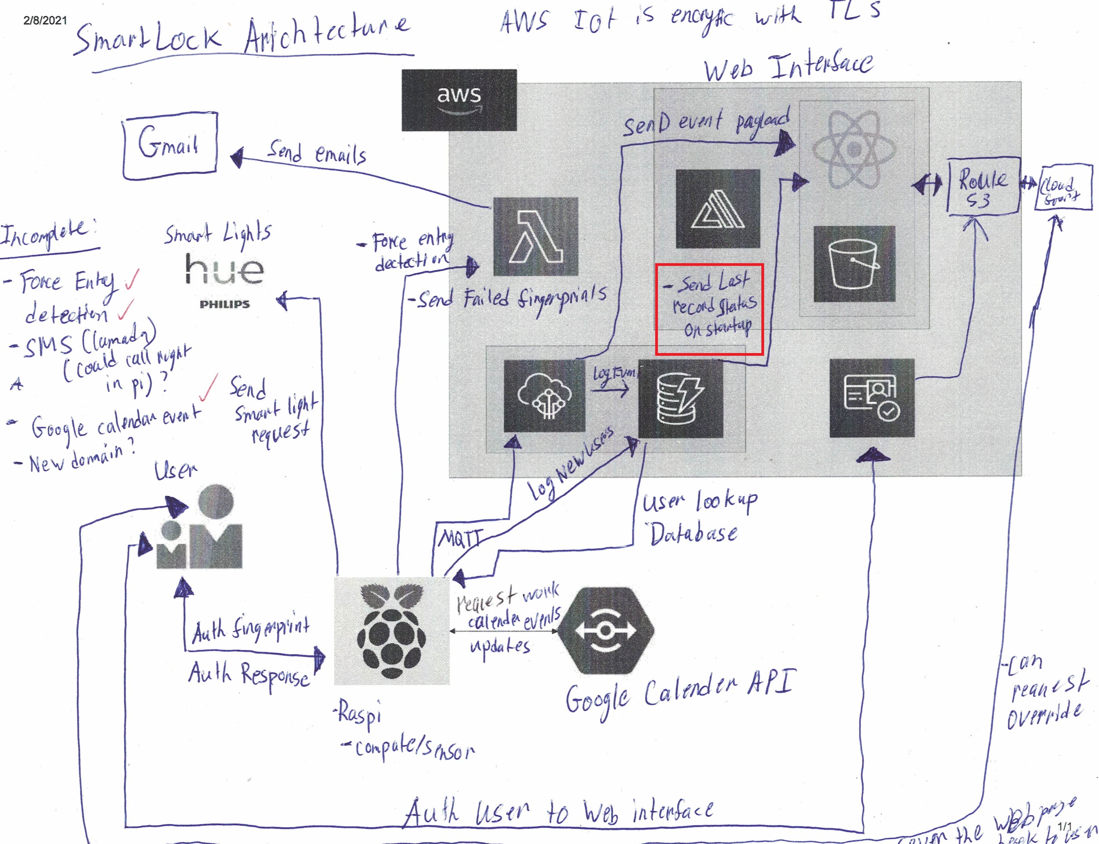
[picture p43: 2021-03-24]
media/Images/Diagrams/Cloud/paper.jpg

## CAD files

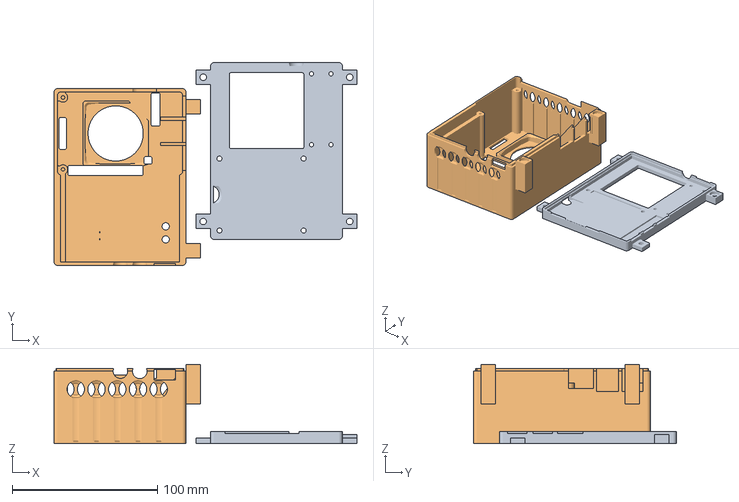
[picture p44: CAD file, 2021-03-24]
cad/Back/Mk3s/Back.3mf
208.9 x 139.9 x 54.7 mm
Door_plate.stl
Top_cover.stl

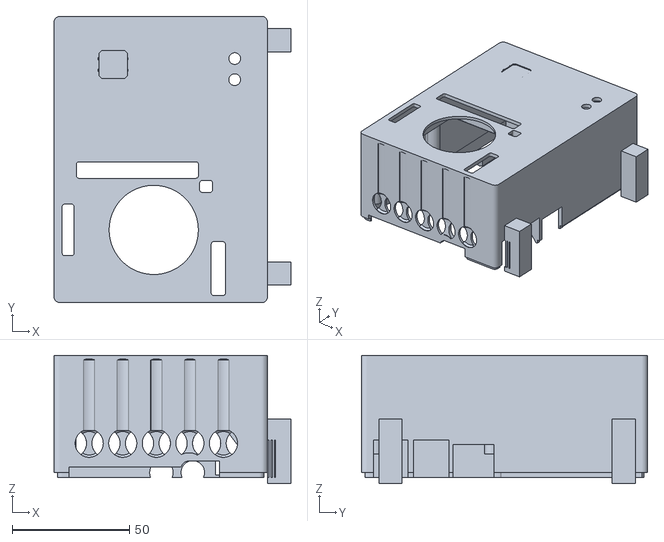
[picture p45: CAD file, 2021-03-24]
cad/Back/Top_cover.stl
101.0 x 122.0 x 54.7

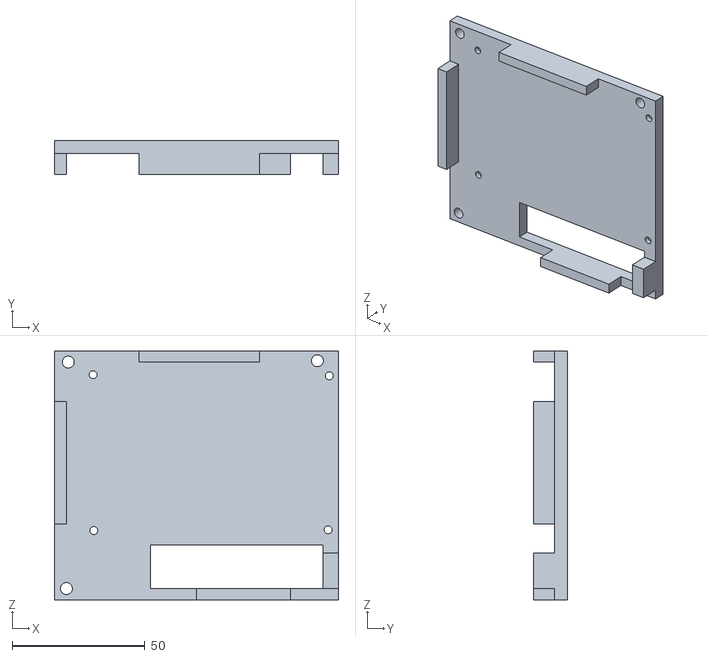
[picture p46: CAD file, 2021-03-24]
cad/Front_IO/Backing.stl
107.1 x 13.0 x 93.7

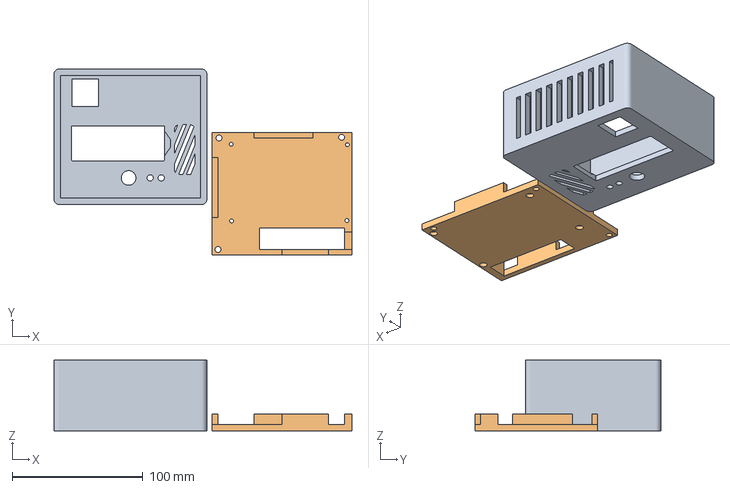
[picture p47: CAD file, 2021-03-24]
cad/Front_IO/Mk3s/Front_IO.3mf
228.3 x 142.5 x 54.3 mm
Cover.stl
Backing.stl

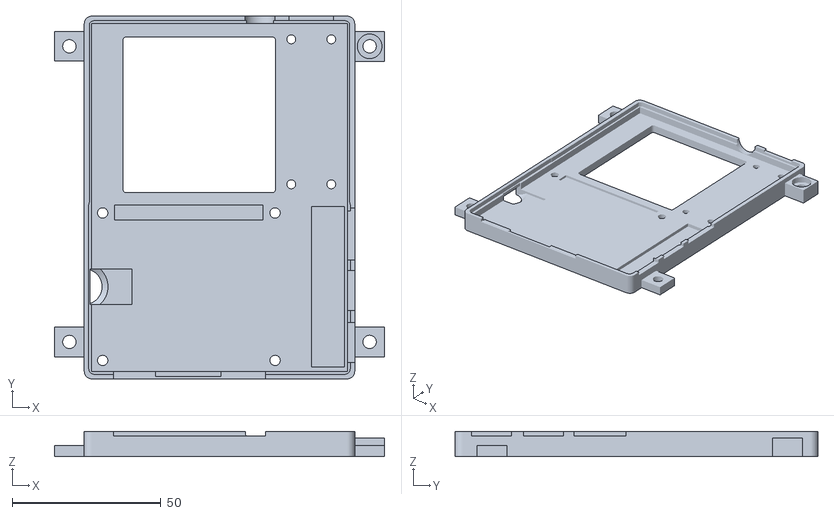
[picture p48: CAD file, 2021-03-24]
cad/Back/Door_plate.stl
111.0 x 122.0 x 8.50

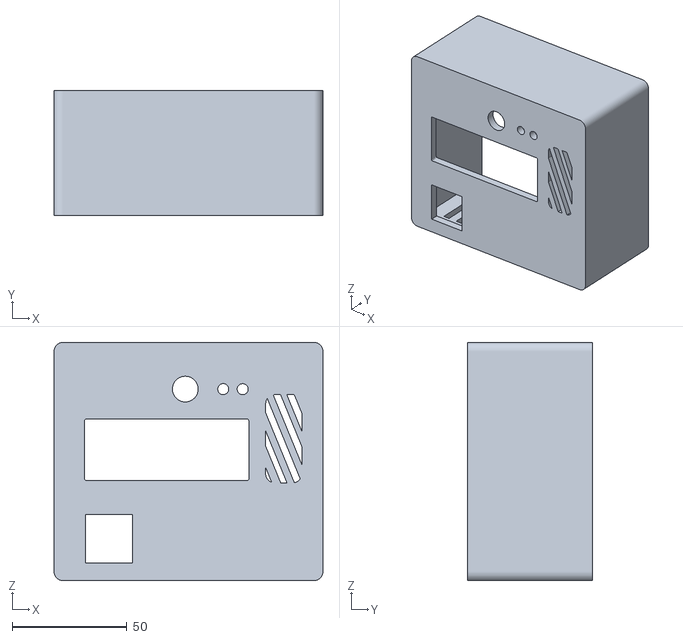
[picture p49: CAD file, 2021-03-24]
cad/Front_IO/Cover.stl
117.1 x 54.3 x 103.8

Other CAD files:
cad/Front_IO/Front_IO.f3z

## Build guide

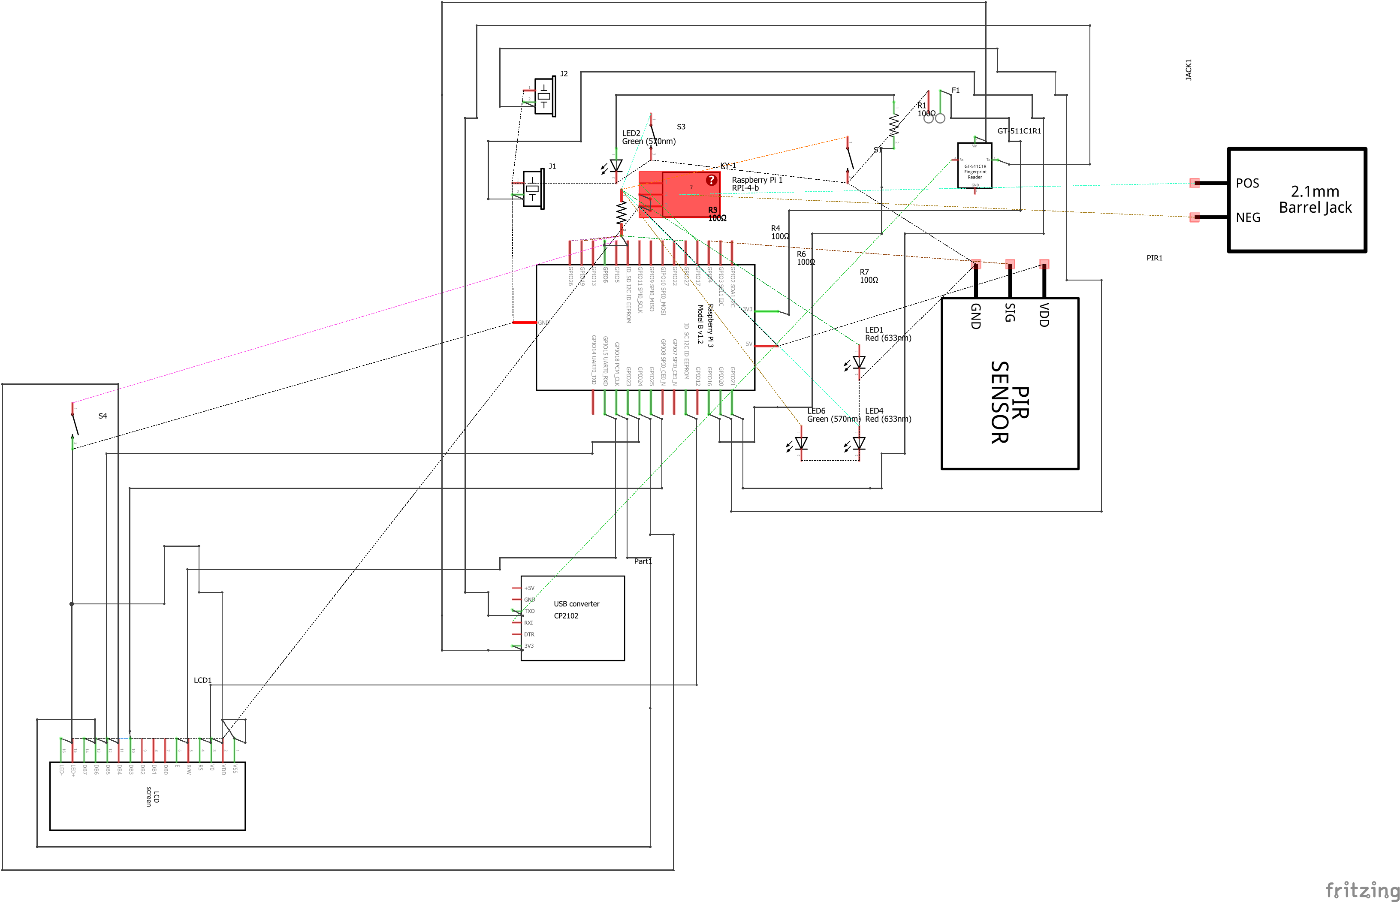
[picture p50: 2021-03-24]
electrical/Images/Lock_wiring_schem.png

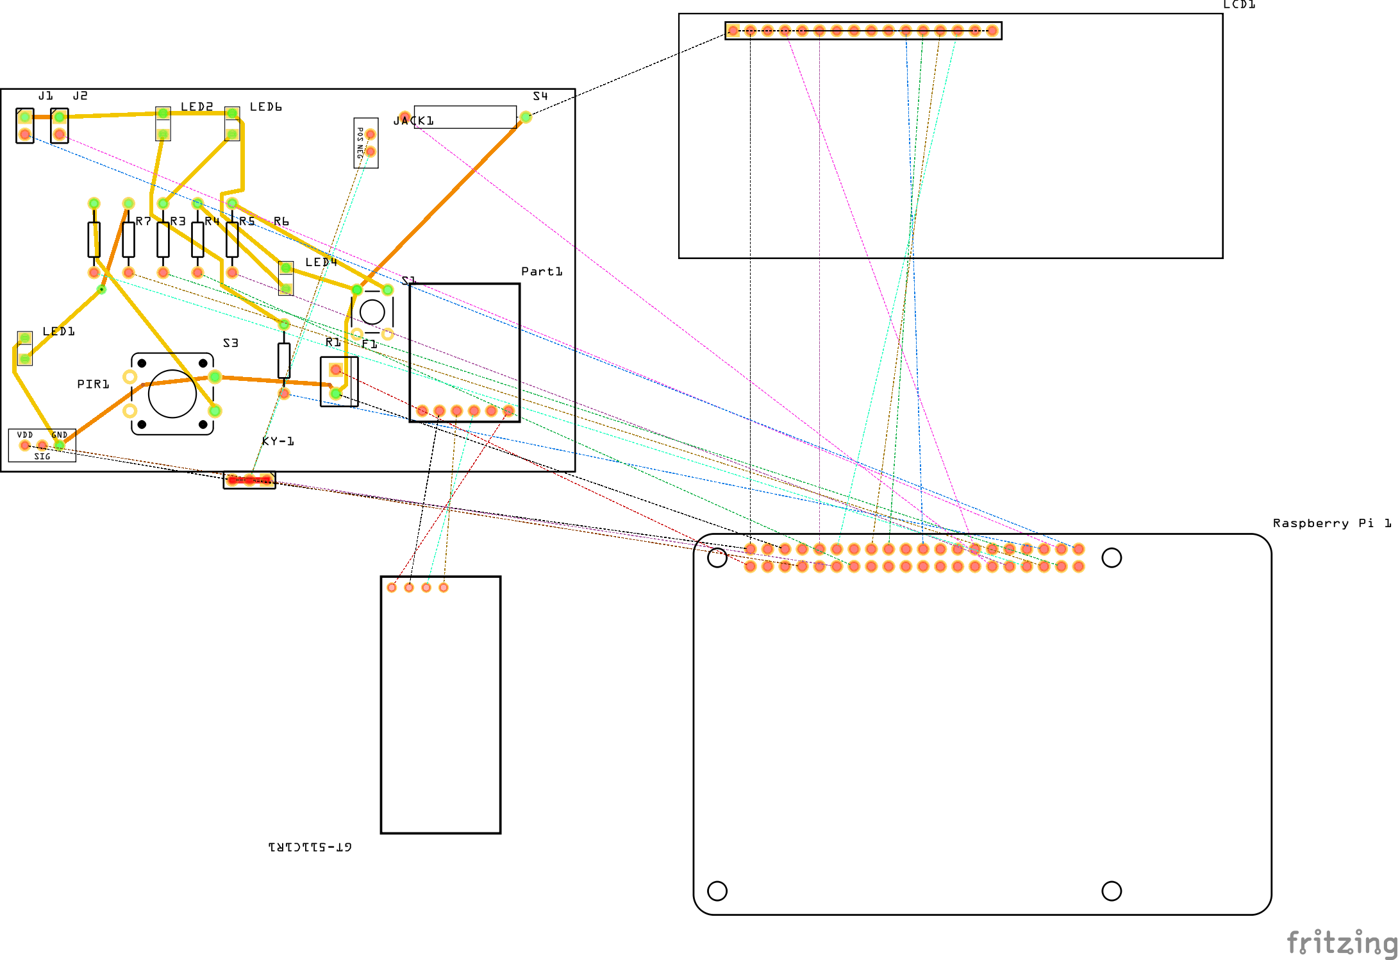
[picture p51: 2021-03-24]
electrical/Images/Lock_wiring_pcb.png

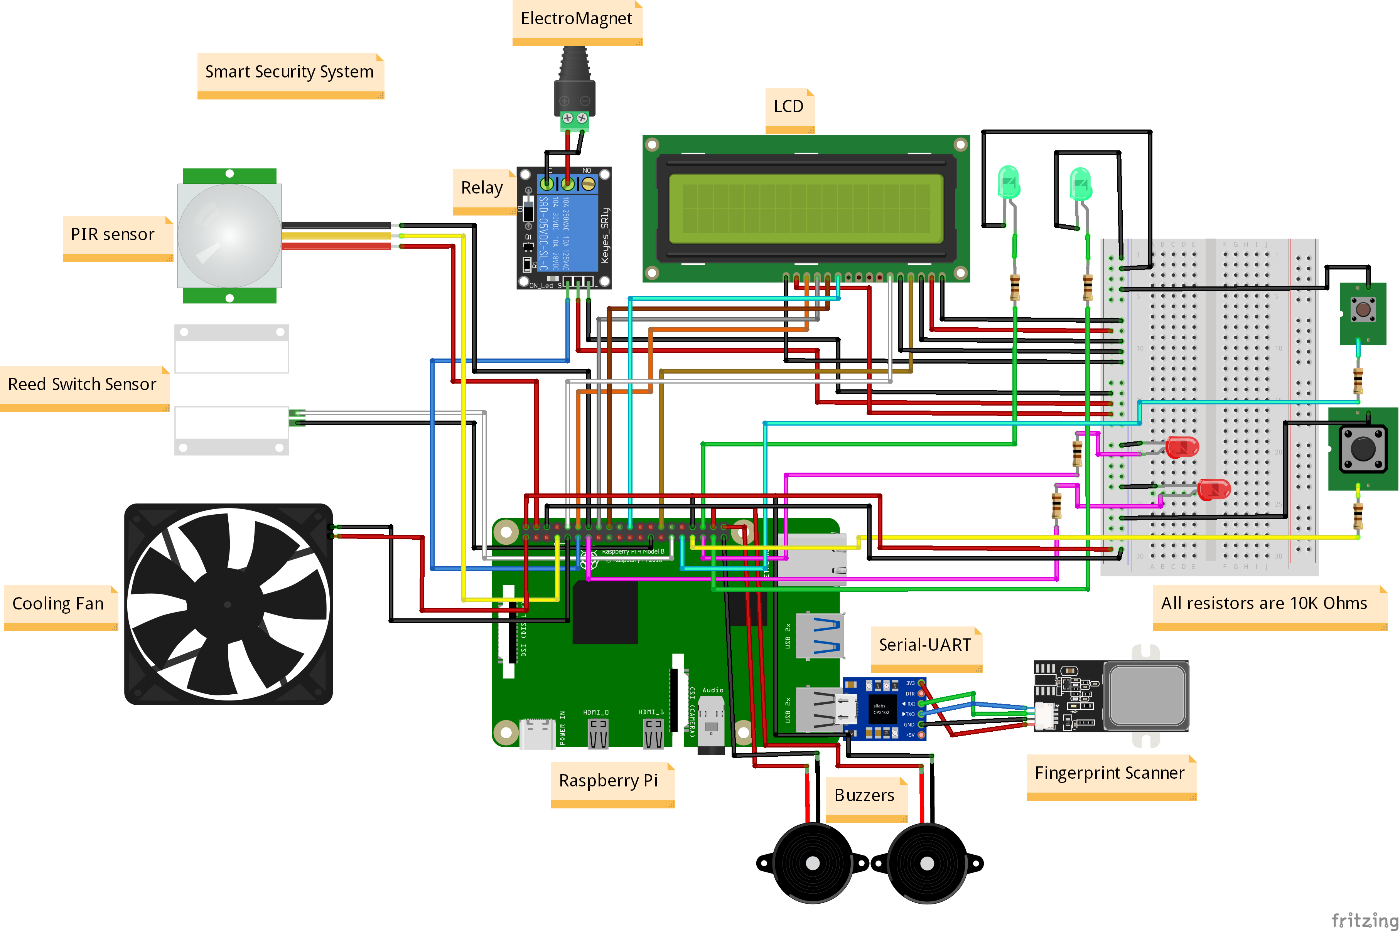
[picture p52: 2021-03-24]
electrical/Images/Lock_wiring_bb_more.png

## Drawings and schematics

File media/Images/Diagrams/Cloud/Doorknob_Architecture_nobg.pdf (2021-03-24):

| IoT Lock | Bedroom Bedroom

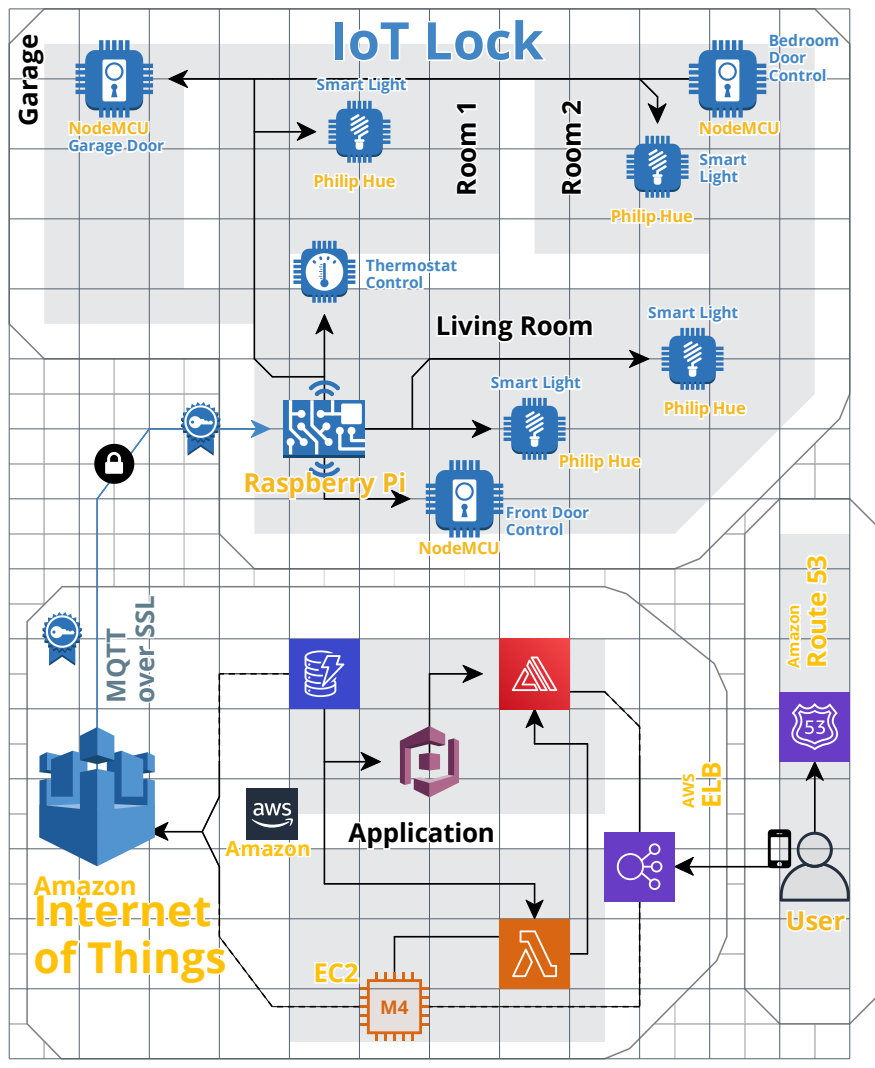
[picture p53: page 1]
Front Door; Garage Door; Internet; NodeMCU; Philip Hue; Control

Door

Smart Light

Philip Hue | | | | | Smart Smart Light Light

Philip Hue

Thermostat Thermostat Control Control
Living Room | | Smart Light

Raspberry Pi

Control

Amazon | Application

Amazon
of Things

User

EC2
M4

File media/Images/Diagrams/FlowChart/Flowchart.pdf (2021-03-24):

# Gather sensor and input data

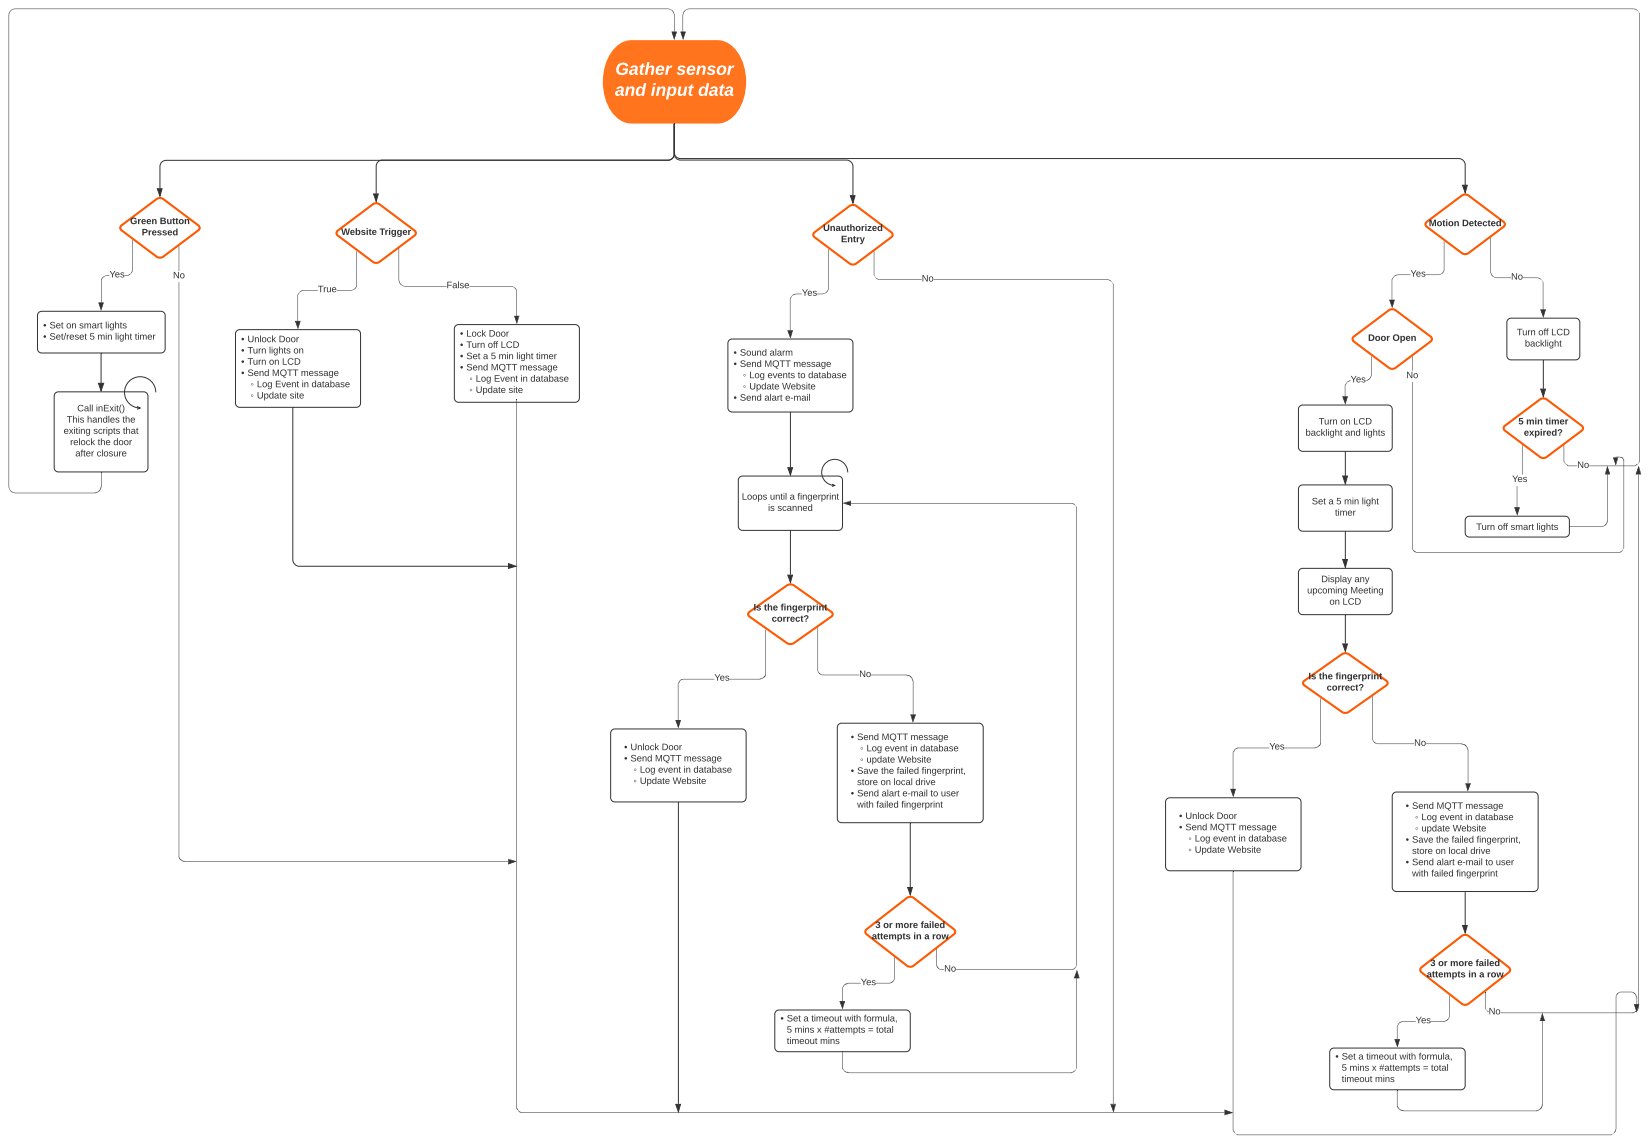
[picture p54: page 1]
Unauthorized Entry; Motion Detected; Website Trigger; Green Button Pressed; Door Open; Yes; 5 min timer expired?; Display any upcoming Meeting on LCD; True; False

- Set on smart lights
- Set/reset 5 min light timer

- Unlock Door
- Turn lights on
- Turn on LCD
- Send MQTT message
- Log Event in database
- Update site

- Lock Door
- Turn off LCD
- Set a 5 min light timer

Turn off LCD
backlight

- Sound alarm
- Log events to database
- Update Website
- Send alart e-mail

Call inExit()
This handles the
exiting scripts that
relock the door
after closure

Turn on LCD
backlight and lights

Loops until a fingerprint
is scanned

Set a 5 min light
timer

Turn off smart lights

Is the fingerprint
correct?

- Log event in database
- update Website
- Save the failed fingerprint,
store on local drive
- Send alart e-mail to user
with failed fingerprint

3 or more failed
attempts in a row

- Set a timeout with formula,
5 mins x #attempts = total
timeout mins

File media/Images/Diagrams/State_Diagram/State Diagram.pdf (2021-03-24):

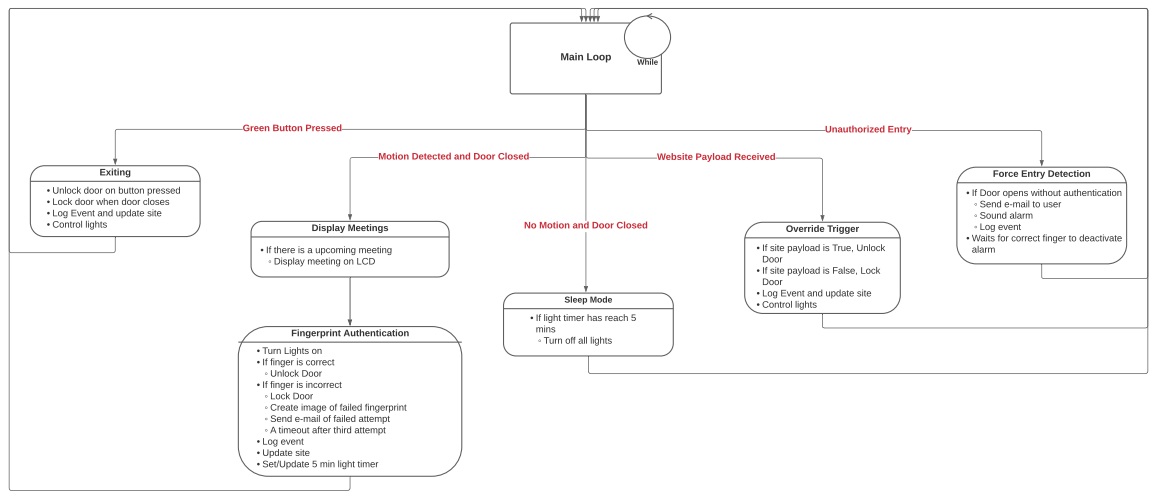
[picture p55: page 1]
Exiting; Sleep Mode; Motion Detected and Door Closed; Website Payload Received; Green Button Pressed; Unauthorized Entry; Display Meetings; Fingerprint Authentication; Main Loop; While

Force Entry Detection
- If Door opens without authentication
- Send e-mail to user
- Sound alarm
- Log event
- Waits for correct finger to deactivate
alarm

- Unlock door on button pressed
- Lock door when door closes
- Log Event and update site
- Control lights

No Motion and Door Closed

Override Trigger
- If site payload is True, Unlock
Door
- If site payload is False, Lock

- If there is a upcoming meeting
- Display meeting on LCD

- If light timer has reach 5
mins
- Turn off all lights

- Turn Lights on
- If finger is correct
- Unlock Door
- If finger is incorrect
- Lock Door
- Create image of failed fingerprint
- Send e-mail of failed attempt
- A timeout after third attempt
- Update site
- Set/Update 5 min light timer

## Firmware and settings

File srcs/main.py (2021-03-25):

#!/usr/bin/env python
# -*- coding: utf-8 -*-
import warnings
import hashlib
from gpiozero import LED
from gpiozero import MotionSensor
from signal import pause
from datetime import datetime
from phue import Bridge
from rgbxy import Converter
from rgbxy import GamutC
import logging
import time
from pyfingerprint.pyfingerprint import PyFingerprint
import RPi.GPIO as GPIO
from libs.custom.lcd_lib import lcd
from libs.custom.lock_lib import lock
from libs.custom.db_lib import db
from libs.custom.awsIOT_lib import awsIOT
from libs.custom.awsIOT_sub import awsIOT_subscribe
from libs.custom.GCAL_lib import Gcal
from libs.custom.mail_lib import mail

#Logging enable
logging.basicConfig()

#Suppress Warnings
warnings.simplefilter('ignore')

#Import e-mail cred
file = open("users.txt", "r")

#Prase cred
user = file.readline().rstrip("\n")
sender=(user.split(";")[0])
pas=(user.split(";")[1])
#comfirm that the server STMP working
if ((sender is not None) and (pas is not None)):
    print("STMP Server is connected")
else:
    print("STMP Server is not connected")

#E-mail receiver(Please enter the receiving E-mail)
receiver = 'example@mail.com'

### Bridge ip (Enter your Philips Hue Bridge IP)
ip = ''

#### AWS Cert Files Publish#### 
awshost = "xxxxxxxxxx-ats.iot.us-west-2.amazonaws.com"      # Endpoint
awsport = 8883                                              # Port no.
clientId = "Smart_Lock_Client"                                     # Thing_Name
thingName = "Smart_Lock_Client"                                    # Thing_Name
caPath = "/home/pi/Desktop/Smart-Doorlock/Components/Cred/Lock_smart/AmazonRootCA1.pem"                    # Root_CA_Certificate_Name
certPath = "/home/pi/Desktop/Smart-Doorlock/Components/Cred/Lock_smart/xxxxxxxxxx-certificate.pem.crt"     # <Thing_Name>.cert.pem
keyPath = "/home/pi/Desktop/Smart-Doorlock/Components/Cred/Lock_smart/xxxxxxxxxx-private.pem.key"          # <Thing_Name>.private.key

#### AWS Cert Files Sub #### 
awshost2 = "xxxxxxxxxx-ats.iot.us-west-2.amazonaws.com"      # Endpoint
awsport2 = 8883                                              # Port no.   
clientId2 = "Override"                                     # Thing_Name
thingName2 = "Override"                                    # Thing_Name
caPath2 = "/home/pi/Desktop/Smart-Doorlock/Components/Cred/Override/AmazonRootCA1.pem"                    # Root_CA_Certificate_Name
certPath2 = "/home/pi/Desktop/Smart-Doorlock/Components/Cred/Override/xxxxxxxxxx-certificate.pem.crt"     # <Thing_Name>.cert.pem
keyPath2 = "/home/pi/Desktop/Smart-Doorlock/Components/Cred/Override/xxxxxxxxxx-private.pem.key"          # <Thing_Name>.private.key

#Objects
thing = awsIOT_lib.awsIOT(awshost, awsport, clientId, thingName, caPath, certPath, keyPath)
sub = awsIOT_sub.awsIOT_subscribe(awshost2, awsport2, clientId2, thingName2, caPath2, certPath2, keyPath2, "Override")
Lock = lock_lib.lock(27, 16, 19, 26, 17, 21, 20, 5, thing, ip)
DB = db_lib.db("Users")
Lcd = Lock.lcd
b = Lock.b#Bridge
c = Lock.c#converter
cal = GCAL_lib.Gcal()
mail = mail_lib.mail(sender, pas)

#Motion
Pir = MotionSensor(4)

#Buzzers
GPIO.setwarnings(False)
GPIO.setmode(GPIO.BCM)
GPIO.setup(Lock.BOpen, GPIO.OUT) #Open
GPIO.setup(Lock.BClose, GPIO.OUT) #Close

#Buzzer
GPIO.setup(6, GPIO.IN, pull_up_down=GPIO.PUD_UP)

#Reader Flag
readerState = False

#Printonce Flag
templates = 0

#Attempt Loop
count = 1

#Timeout
timeout = 1

#Flag for overide
happenOnce = False

#timeout period
period = 5

#TimeOut function
def timeOut(timeout):
    total = (period*timeout)
    totalTime = total - 1
    for i in range (total):
        for j in range (60):
            new =(str(totalTime-i) + ":" + str(59-j))
            time.sleep(1)
            Lcd.lcd_string('Timeout Left:', 1)
            Lcd.lcd_string(new, 2)
            print("Timeout: " + new)

#Set the lights to white
b.set_light(1, 'on', True)
b.set_light(2, 'on', True)
b.set_light(1, 'xy', c.rgb_to_xy(253, 244, 220))
b.set_light(2, 'xy', c.rgb_to_xy(253, 244, 220))
b.set_light(1, 'on', False)
b.set_light(2, 'on', False)

#Colour Var
RED = (255, 0, 0)
Green = (0, 255, 0)
White = (253, 244, 220)

#5 Min timer
timer = 300

#Last recored timestamp
ts=0

#Timestamp expire
ts_expire = Lock.timestamped

#Lock right at the beginnig
Lock.SetLock()

#Set the alarm off
GPIO.output(Lock.BClose, False)
GPIO.output(Lock.BOpen, False)

#Main Loop
try:
    while True:

        #This will trigger the Override function from the react site
        if (sub.getPayload() == "true"):
            while True:
                # This flag will only let this trigger loop once
                if (happenOnce == False):
                    now = datetime.now()
                    ts = int(now.timestamp())
                    ts_expire = ts + timer
                    date = str(now.date())
                    unix = int(datetime.timestamp(now))
                    dt_string = now.strftime("%d/%m/%Y_%H:%M:%S")
                    userID = "Override Trigger"
                    finger = "Static Site"
                    accuracyScore = -1
                    print("Override trigger Activated")
                    Lock.status("Unlock", now)
                    #Update display
                    Lcd.backlight(True)
                    Lcd.lcd_string("Override Trigger", 1)
                    Lcd.lcd_string("Unlock", 2)
                    #Turn Light on
                    b.set_light(1, 'on', True)
                    b.set_light(2, 'on', True)
                    #Set Lights to Green
                    b.set_light(1, 'xy', c.rgb_to_xy(0, 250, 0))
                    b.set_light(2, 'xy', c.rgb_to_xy(0, 250, 0))
                    time.sleep(1)
                    #Set back to white
                    b.set_light(1, 'xy', c.rgb_to_xy(253, 244, 220))
                    b.set_light(2, 'xy', c.rgb_to_xy(253, 244, 220))
                    thing.publish("Smart_Lock", thing.createPayload(userID, finger, accuracyScore, "Unlocked", dt_string, unix, date))
                    happenOnce = True
                    del now

                # datetime object containing current date and time
                now = datetime.now()
                ts = int(now.timestamp())
                del now

                #Compares the time now to the 5 min timer
                if ((ts - ts_expire)>=0):
                    #Turn off all lights
                    Lcd.backlight(False)
                    b.set_light(1, 'on', False)
                    b.set_light(2, 'on', False)
                    
                #If the door opens
                if(Pir.value == True):
                    #Set the lights to white
                    b.set_light(1, 'on', True)
                    b.set_light(2, 'on', True)
                    b.set_light(1, 'xy', c.rgb_to_xy(253, 244, 220))
                    b.set_light(2, 'xy', c.rgb_to_xy(253, 244, 220))
                    now = datetime.now()
                    ts = int(now.timestamp())
                    ts_expire = ts + timer
                    del now


                #Reset the timer if the door is closed and there is motion
                if ((Pir.value == True) and (Lock.getReed() == 0)):
                    #Update display
                    Lcd.backlight(True)
                    Lcd.lcd_string("Welcome", 1)
                    Lcd.lcd_string("Door Unlocked", 2)
                    #Set the lights to white
                    b.set_light(1, 'on', True)
                    b.set_light(2, 'on', True)
                    b.set_light(1, 'xy', c.rgb_to_xy(253, 244, 220))
                    b.set_light(2, 'xy', c.rgb_to_xy(253, 244, 220))
                    now = datetime.now()
                    ts = int(now.timestamp())
                    ts_expire = ts + timer
                    del now

                #Wait to listen for the command to be sent
                if (sub.getPayload() == "false"):
                    now = datetime.now()
                    date = str(now.date())
                    unix = int(datetime.timestamp(now))
                    dt_string = now.strftime("%d/%m/%Y_%H:%M:%S")
                    userID = "Override Trigger"
                    finger = "Static Site"
                    print("Override trigger Deactivated")
                    #Update display
                    Lcd.backlight(True)
                    Lcd.lcd_string("Override Trigger", 1)
                    Lcd.lcd_string("Locked", 2)
                    #Unlock
                    Lock.status("Lock", now)
                    #Turn Light on
                    b.set_light(1, 'on', True)
                    b.set_light(2, 'on', True)
                    #Set Lights to Red
                    b.set_light(1, 'xy', c.rgb_to_xy(250, 0, 0))
                    b.set_light(2, 'xy', c.rgb_to_xy(250, 0, 0))
                    time.sleep(1)
                    #Set back to white
                    b.set_light(1, 'xy', c.rgb_to_xy(253, 244, 220))
                    b.set_light(2, 'xy', c.rgb_to_xy(253, 244, 220))
                    thing.publish("Smart_Lock", thing.createPayload(userID, finger, accuracyScore, "Locked", dt_string, unix, date))
                    happenOnce = False
                    del now
                    #Return back to the the other states
                    break

        #This will trigger a exit pushbutton(Green) for exiting from the inside
        if (GPIO.input(6) == False):
            #Set lights on
            b.set_light(1, 'on', True)
            b.set_light(2, 'on', True)
            b.set_light(1, 'xy', c.rgb_to_xy(253, 244, 220))
            b.set_light(2, 'xy', c.rgb_to_xy(253, 244, 220))
            Lock.inExit() #while loop
            ts_expire = Lock.timestamped

        #Force Entry detection (if the door with any authentication)
        if ((Lock.getReed() == 1)):#Door is open

            # Sound alarm, If both go off the frequency cancel each other out
            #GPIO.output(Lock.BClose, True)
            GPIO.output(Lock.BOpen, True)
            
            #Log event
            now = datetime.now() #datetime object containing current date and time
            date = str(now.date())
            unix = int(datetime.timestamp(now))
            dt_string = now.strftime("%d/%m/%Y_%H:%M:%S")
            userID = 'Force Entry'
            finger = "None"
            accuracyScore = -1
            status = Lock.getReedStatus()
            thing.publish("Smart_Lock", thing.createPayload(userID, finger, accuracyScore, Lock.getReedStatus(), dt_string, unix, date))

            #Send e-mail
            mail.sendMessage(receiver, "Forced Entry: " + dt_string, "There was a Forced Entry Detected at " +  dt_string + ". Please go reset the door alarm by fingerprint authentication and asset situation." )

            #Delete 
            del now

            #Wait for correct fingerprint authentication
            try:  #Intialize finger print reader
                f = PyFingerprint('/dev/ttyUSB0', 57600, 0xFFFFFFFF, 0x00000000)
                
                if ( f.verifyPassword() == False ):
                    raise ValueError('The given fingerprint sensor password is wrong!')

            except Exception as e:
                print('The fingerprint sensor could not be initialized!')
                print('Exception message: ' + str(e))
                #Only comment out if you are getting packet corruption
                #exit(1)
            ## Gets some sensor information
            if (templates == 0):
                print('Currently used templates: ' + str(f.getTemplateCount()) +'/'+ str(f.getStorageCapacity()))
                templates=1
            
            #Turn on LCD
            Lcd.backlight(True)
            Lcd.lcd_string('Waiting for', 1)
            Lcd.lcd_string('finger...', 2)

            #Enter a loop to wait for a finger print
            while True:
                #Reset lights back to white
                b.set_light(1, 'on', True)
                b.set_light(2, 'on', True)
                b.set_light(1, 'xy', c.rgb_to_xy(253, 244, 220))
                b.set_light(2, 'xy', c.rgb_to_xy(253, 244, 220))

                #Display to place finger on scanner
                Lcd.lcd_string('Waiting for', 1)
                Lcd.lcd_string('finger...', 2)

                if (f.readImage() == True): #READ if finger is read
                    Lcd.backlight(True)
                    Lcd.lcd_string("Attempt #", 1)
                    Lcd.lcd_string(str(count), 2)
                    ## Converts read image to characteristics and stores it in charbuffer 1
                    f.convertImage(0x01)

                    ## Searchs template
                    result = f.searchTemplate()

                    #Selecting index for match
                    positionNumber = result[0]
                    accuracyScore = result[1]

                    #Check buffer template against stored template
                    if (positionNumber != -1 and accuracyScore >= 50): #Finger is in database if true
                        response = DB.getItem(positionNumber)
                        userID = response["userID"]
                        finger = response["finger"]

                        #Turn off alarm
                        #GPIO.output(Lock.BClose, False)
                        GPIO.output(Lock.BOpen, False)

                        #Display to LCD that fingerprint is correct
                        Lcd.backlight(True)
                        Lcd.lcd_string("Fingerprint Correct", 1)
                        Lcd.lcd_string("ID:" + userID, 2)

                        # datetime object containing current date and time
                        now = datetime.now()
                        dt_string = now.strftime("%d/%m/%Y_%H:%M:%S")
                        date = str(now.date())
                        unix = int(datetime.timestamp(now))

                        #Upload data to IOT CORE
                        thing.publish("Smart_Lock", thing.createPayload(userID, finger, accuracyScore, "Reset Alarm Correct", dt_string, unix, date))
                        
                        #Set Lights to Green
                        b.set_light(1, 'xy', c.rgb_to_xy(0, 250, 0))
                        b.set_light(2, 'xy', c.rgb_to_xy(0, 250, 0))

                        #Send e-mail
                        mail.sendMessage(receiver, "Alarm Reset Correctly", "The alarm was reset by: " + userID + " at " + dt_string + " with the finger " + finger + " and with the accuracy of " + str(accuracyScore) + "%" )
                        
                        count = 1
                        timeout =1
                        # erase stored results in memory
                        del now
                        del result
                        del positionNumber
                        del accuracyScore
                        break

                    #Fingerprint authentication
                    else: 
                        #Set Lights to Red
                        b.set_light(1, 'xy', c.rgb_to_xy(250, 0, 0))
                        b.set_light(2, 'xy', c.rgb_to_xy(250, 0, 0))

                        # Records the fail thumb print and stores it locally
                        print('Downloading image (this take a while)...')

                        #Display to LCD that fingerprint is correct
                        Lcd.backlight(True)
                        Lcd.lcd_string("Fingerprint Fail", 1)
                        Lcd.lcd_string("Piss Off", 2)

                        # datetime object containing current date and time
                        now = datetime.now()
                        dt_string = now.strftime("%d/%m/%Y_%H:%M:%S")
                        d_string = now.strftime("%d_%m_%Y-%H_%M_%S")
                        date = str(now.date())
                        unix = int(datetime.timestamp(now))
                        userID = "Alarm Failed"
                        finger = "Recored"
                        status = Lock.getReedStatus() + ", Reset Alarm Failed"

                        #Downlaod Fingerprint
                        imageDestination = '/home/pi/Pictures/failPrints/' + d_string + 'fingerprint.bmp'
                        f.downloadImage(imageDestination)
                        
                        #Less then 3 attempts
                        if (count < 3):
                            #Upload data to IOT CORE
                            thing.publish("Smart_Lock", thing.createPayload(userID, finger, accuracyScore, status, dt_string, unix, date))

                            # E-mail
                            mail.sendItem(receiver, ("This is attempt number on Force Entry Reset: " + str(count)), ("This was capture at " + dt_string + " and Image stored locally at " + imageDestination), imageDestination)
                            print('The image was saved to "' + imageDestination + "at the time: " + d_string + '".')
                        
                        #This is for more then 3 attempts
                        if (count >= 3):
                            del now
                            # datetime object containing current date and time
                            now = datetime.now()
                            dt_string = now.strftime("%d/%m/%Y_%H:%M:%S")
                            thing.publish("Smart_Lock", thing.createPayload(userID, str(count), accuracyScore, status, dt_string, unix, date))
                            #E-mail
                            mail.sendItem(receiver, ("This is attempt number on Force Entry Reset: " + str(count)), ("A timeout was trigger at the attempt #" + str(count) + ", a timeout of " + str(timeout*5) + " mins has been set. This was capture at " + dt_string + " and Image stored locally at " + imageDestination), imageDestination)
                            print('The image was saved to "' + imageDestination + "at the time: " + d_string + '".')

                            #Timeout 
                            timeOut(timeout)

                            #Timeout counter
                            timeout += 1
                            
                        #Counter
                        count += 1    

                        #Set lights on and back to white
                        b.set_light(1, 'on', True)
                        b.set_light(2, 'on', True)
                        b.set_light(1, 'xy', c.rgb_to_xy(253, 244, 220))
                        b.set_light(2, 'xy', c.rgb_to_xy(253, 244, 220))

                        # erase stored results in memory
                        del now
                        del result
                        del positionNumber
                        del accuracyScore

                #Used to slow down the scanning of the fingerprint sensor
                time.sleep(0.3)

        # if (no motion and door is closed)
        if ((Pir.value == False) and (Lock.getReed() == 0)):
            Lcd.backlight(False)

            # datetime object containing current date and time
            now = datetime.now()
            ts = int(now.timestamp())
            del now
            if ((ts - ts_expire)>=0):
                #Set lights off
                b.set_light(1, 'on', False)
                b.set_light(2, 'on', False)

        # if (motion and door is closed)
        if ((Pir.value == True) and (Lock.getReed() == 0)):
            Lcd.backlight(True)
            #Set lights on
            b.set_light(1, 'on', True)
            b.set_light(2, 'on', True)
            b.set_light(1, 'xy', c.rgb_to_xy(253, 244, 220))
            b.set_light(2, 'xy', c.rgb_to_xy(253, 244, 220))

            #Make sure Door is Lock
            Lock.SetLock()

            # datetime object containing current date and time
            now = datetime.now()
            sysDate = now.strftime("%Y-%m-%d")
            sysTime = now.strftime("%H:%M:%S")
            ts = int(now.timestamp())
            ts_expire = ts + timer
            del now
            try:  #Intialize finger print reader
              f = PyFingerprint('/dev/ttyUSB0', 57600, 0xFFFFFFFF, 0x00000000)
              
              if ( f.verifyPassword() == False ):
                raise ValueError('The given fingerprint sensor password is wrong!')

            except Exception as e:
                print('The fingerprint sensor could not be initialized!')
                print('Exception message: ' + str(e))
                #Only comment out if you are getting packet corruption
                #exit(1)

            ## Gets some sensor information
            if (templates == 0):
              print('Currently used templates: ' + str(f.getTemplateCount()) +'/'+ str(f.getStorageCapacity()))
              templates=1
            readerState = True #FLAG

            #Call the Google calendar api to trigger for the next same day event
            calEvent = cal.nextEvent(sysDate)
            
            if calEvent is None:
                Lcd.lcd_string('Waiting for', 1)
                Lcd.lcd_string('finger...', 2)
            elif ((sysTime >= calEvent["Start"]) and (sysTime <= calEvent["End"])):
                calstart = calEvent["Start"].rstrip(":")
                calend = calEvent["End"].rstrip(":")
                Lcd.lcd_string('In Meeting', 1)
                Lcd.lcd_string(calstart + " - " + calend, 2)
                time.sleep(1)
                Lcd.lcd_string("Get off my",1)
                Lcd.lcd_string("Lawn!!!!!!!!", 2)
                time.sleep(1)
            else:
                Lcd.lcd_string('Waiting for', 1)
                Lcd.lcd_string('finger...', 2)
        if(readerState == True):
            readerState = False
            if (f.readImage() == True): #READ if finger is read
                Lcd.backlight(True)
                Lcd.lcd_string("Attempt #", 1)
                Lcd.lcd_string(str(count), 2)
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

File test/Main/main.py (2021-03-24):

#!/usr/bin/env python
# -*- coding: utf-8 -*-

import hashlib
from gpiozero import LED, Button
from gpiozero import MotionSensor
from signal import pause
import time
from pyfingerprint.pyfingerprint import PyFingerprint
import RPi.GPIO as GPIO


# Define GPIO to LCD mapping
RED = 27
GREEN = 16
REDIN = 19
GREENIN = 26
LOCK = 17
BUZZO = 21
BUZZC = 20
LCD_RS = 7
LCD_E  = 8
LCD_D4 = 25
LCD_D5 = 24
LCD_D6 = 23
LCD_D7 = 18
LED_ON = 15
pir = MotionSensor(4)
YBUTT = 13
GBUTT = 6
YBUTT2 = Button(13)
GBUTT2 = Button(6)
RELAY = LED(17)
LED_ON2 = LED(15)
Reed = 5
# Define some device constants
LCD_WIDTH = 16    # Maximum characters per line
LCD_CHR = True
LCD_CMD = False

LCD_LINE_1 = 0x80 # LCD RAM address for the 1st line
LCD_LINE_2 = 0xC0 # LCD RAM address for the 2nd line

# Timing constants
E_PULSE = 0.0005
E_DELAY = 0.0005

#Reader Flag
readerState = False

def setup():
  # Main setup block
  
  GPIO.setwarnings(False)
  GPIO.setmode(GPIO.BCM)       # Use BCM GPIO numbers
  GPIO.setup(LCD_E, GPIO.OUT)  # E
  GPIO.setup(LCD_RS, GPIO.OUT) # RS
  GPIO.setup(LCD_D4, GPIO.OUT) # DB4
  GPIO.setup(LCD_D5, GPIO.OUT) # DB5
  GPIO.setup(LCD_D6, GPIO.OUT) # DB6
  GPIO.setup(LCD_D7, GPIO.OUT) # DB7
  GPIO.setup(LOCK, GPIO.OUT) #Switch
  GPIO.setup(LED_ON, GPIO.OUT) # Backlight enable
  GPIO.setup(RED, GPIO.OUT) #Red
  GPIO.setup(GREEN, GPIO.OUT) #Green
  GPIO.setup(BUZZO, GPIO.OUT) #Opening Buzzer
  GPIO.setup(BUZZC, GPIO.OUT) #Closing Buzzer
  GPIO.setup(REDIN, GPIO.OUT) #Red inside
  GPIO.setup(GREENIN, GPIO.OUT) #Green inside
  GPIO.setup(YBUTT, GPIO.IN, pull_up_down=GPIO.PUD_UP) #Yellow Button
  GPIO.setup(GBUTT, GPIO.IN, pull_up_down=GPIO.PUD_UP) #Green Button
  GPIO.setup(Reed, GPIO.IN) #Reed Switch

  # Initialise display
  lcd_init()

def lcd_init():
  # Initialise display
  lcd_byte(0x33,LCD_CMD) # 110011 Initialise
  lcd_byte(0x32,LCD_CMD) # 110010 Initialise
  lcd_byte(0x06,LCD_CMD) # 000110 Cursor move direction
  lcd_byte(0x0C,LCD_CMD) # 001100 Display On,Cursor Off, Blink Off
  lcd_byte(0x28,LCD_CMD) # 101000 Data length, number of lines, font size
  lcd_byte(0x01,LCD_CMD) # 000001 Clear display
  time.sleep(E_DELAY)

def lcd_byte(bits, mode):
  # Send byte to data pins
  # bits = data
  # mode = True  for character
  #        False for command

  GPIO.output(LCD_RS, mode) # RS

  # High bits
  GPIO.output(LCD_D4, False)
  GPIO.output(LCD_D5, False)
  GPIO.output(LCD_D6, False)
  GPIO.output(LCD_D7, False)
  if bits&0x10==0x10:
    GPIO.output(LCD_D4, True)
  if bits&0x20==0x20:
    GPIO.output(LCD_D5, True)
  if bits&0x40==0x40:
    GPIO.output(LCD_D6, True)
  if bits&0x80==0x80:
    GPIO.output(LCD_D7, True)

  # Toggle 'Enable' pin
  lcd_toggle_enable()

  # Low bits
  GPIO.output(LCD_D4, False)
  GPIO.output(LCD_D5, False)
  GPIO.output(LCD_D6, False)
  GPIO.output(LCD_D7, False)
  if bits&0x01==0x01:
    GPIO.output(LCD_D4, True)
  if bits&0x02==0x02:
    GPIO.output(LCD_D5, True)
  if bits&0x04==0x04:
    GPIO.output(LCD_D6, True)
  if bits&0x08==0x08:
    GPIO.output(LCD_D7, True)

  # Toggle 'Enable' pin
  lcd_toggle_enable()

def lcd_toggle_enable():
  # Toggle enable
  time.sleep(E_DELAY)
  GPIO.output(LCD_E, True)
  time.sleep(E_PULSE)
  GPIO.output(LCD_E, False)
  time.sleep(E_DELAY)

def lcd_string(message,line):
  # Send string to display
  message = message.ljust(LCD_WIDTH," ")

  lcd_byte(line, LCD_CMD)

  for i in range(LCD_WIDTH):
    lcd_byte(ord(message[i]),LCD_CHR)
    
def access():
      GPIO.output(LOCK, False)
      GPIO.output(BUZZO, True)
      time.sleep(0.2)
      GPIO.output(BUZZO, False)
      lcd_string('Access Granted',LCD_LINE_1)
      lcd_string('Welcome!',LCD_LINE_2)
      GPIO.output(BUZZO, True)
      time.sleep(0.2)
      GPIO.output(BUZZO, False)
      GPIO.output(RED, False)
      GPIO.output(REDIN, False)
      GPIO.output(GREEN, True)
      GPIO.output(GREENIN, True)
      time.sleep(1.5)
      if (positionNumber == 0):        
        newPos = "Kevin`s Index"
      elif (positionNumber == 1):
        newPos ="Kevin`s Thumb"
        lcd_string('ID#' + str(newPos),LCD_LINE_1)
        lcd_string('Accuracy: ' + str(accuracyScore),LCD_LINE_2)
        time.sleep(3)
      elif (positionNumber == 2):
        newPos ="Eden`s Index"
        lcd_string('ID#' + str(newPos),LCD_LINE_1)
        lcd_string('Accuracy: ' + str(accuracyScore),LCD_LINE_2)
        time.sleep(3)
      #Door open
      lcd_string('Door Status:',LCD_LINE_1)
      lcd_string('UNLOCKED',LCD_LINE_2)
      time.sleep(5)
      GPIO.output(GREEN, False)
      GPIO.output(GREENIN, False)
      GPIO.output(LED_ON, False) #LCD OFF
      while(GPIO.input(Reed) == 1):
          pass
      relock()
        
def relock():
  
      GPIO.output(LOCK, True)#Lock Lock
      GPIO.output(LED_ON, True) #LCD ON
      lcd_string('Door Status:',LCD_LINE_1)
      lcd_string('LOCKED',LCD_LINE_2)
      GPIO.output(RED, True)
      GPIO.output(REDIN, True)
      GPIO.output(GREEN, False)
      GPIO.output(GREENIN, False)
      GPIO.output(BUZZC, True)
      time.sleep(0.3)
      GPIO.output(BUZZC, False)
      time.sleep(0.3)
      GPIO.output(BUZZC, True)
      time.sleep(0.3)
      GPIO.output(BUZZC, False)
      time.sleep(0.3)
      GPIO.output(REDIN, False)
      GPIO.output(GREENIN, False)

def lock1():
      GPIO.output(LOCK, True)#Lock Lock
      GPIO.output(RED, True)
      GPIO.output(REDIN, False)
      GPIO.output(GREEN, False)
      GPIO.output(GREENIN, False)

def inExit():
      GPIO.output(LOCK, False) #unlock door
      GPIO.output(REDIN, False)
      GPIO.output(GREENIN, True)
      lcd_string('Door Status:',LCD_LINE_1)
      lcd_string('UNLOCKED',LCD_LINE_2)
      time.sleep(3)
      GPIO.output(REDIN, False)
      GPIO.output(GREENIN, False)
      GPIO.output(RED, False)
      GPIO.output(GREEN, False)
      while(GPIO.input(Reed) == 1):
          pass
      relock()
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

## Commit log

2021-03-24 First Commit
    This is the first commit and new repo because of old commit from last repo.
    [Back.3mf, Backing.stl, Cover.stl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]
2021-03-24 New Folders
    [Back.3mf, Backing.stl, Cover.stl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]
